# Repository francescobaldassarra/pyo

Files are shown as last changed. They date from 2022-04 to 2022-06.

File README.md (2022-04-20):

# Pyo
Robotic platform for emotional research in the human-robot interaction field.

-- EN --
Pyo is a low-cost robotic platform aimed at researchers working in the field of Human Robot Interaction. It is based on the Arduino platform and additive manufacturing production process (3D printing FDM). It is an easy-to-manage, accessible and customisable tool to research used to test emotional and expressive capacity of a social robot. The current version of Pyo is developed with a focus on non-verbal communication using facial expressions, auditory icons and body language.

The purpose of the research is to investigate how robots’ non-verbal communication can trigger an emotional response and to what extent expression and feeling are connected in a human-robot interaction.

-- IT --
Pyo è una piattaforma rrobotica low-cost per ricercatori che lavorano nel campo dell'interazione uomo-robot. Si basa sulla piattaforma Arduino e sul processo di produzione additiva (stampa 3D FDM). È uno strumento di ricerca facile da gestire, accessibile e personalizzabile utilizzato per testare le capacità emotive ed espressive di un robot sociale. La versione attuale di Pyo è sviluppata con un focus sulla comunicazione non-verbale utilizzando espressioni facciali, icone uditive e linguaggio del corpo.

Lo scopo della ricerca è quello di indagare come la comunicazione non verbale dei robot può innescare una risposta emotiva e in che misura l'espressione e il sentimento sono collegati in un'interazione uomo-robot.

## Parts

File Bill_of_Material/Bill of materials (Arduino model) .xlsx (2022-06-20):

What I need to reproduce Pyo platform with Arduino
Name | Quantity | Price (Eur) | Link (approximate) | Note
Arduino Mega 2560 | 1 | 39.9 | https://www.amazon.com/ARDUINO-MEGA-2560-REV3-A000067/dp/B0046AMGW0
Mega Proto shield | 1 | 5.8 | https://www.amazon.com/Treedix-Prototype-Solderable-BreadBoard-Compatible/dp/B08G1G7YDZ
Audio amplifier module digital 3W 5V | 1 | 5.9 | https://www.amazon.com/HiLetgo-Amplifier-Dual-Channel-Amplifiers-Potentiometer/dp/B01DKAI51M
MP3 Player module MicroSD | 1 | 5.9 | https://www.amazon.com/DFPlayer-Player-YX5200-Support-Arduino/dp/B07BDD8BF3
Micro SD (>1gb) | 1 | 4.4
IR emote Control, Sensor Board | 1 | 6.2 | https://www.amazon.com/KOOBOOK-Infrared-Wireless-Control-Receiver/dp/B07S67SFSF
Speaker | 1 | 7.1 | https://www.amazon.com/Fielect-Magnet-Speaker-Internal-Rectangle/dp/B08276866N
Servo motor MG996R | 4 | 24.7 | https://www.amazon.com/DaFuRui-Digital-Compatible-Arduino-Helicopter/dp/B09P18XNK2
Led matrix 8x32 RGB | 1 | 20.2 | https://www.amazon.com/BTF-LIGHTING-Individual-Addressable-Flexible-Controllers/dp/B088BTXHRG
Switch on/off | 1 | 1
Axial bearing 25x47x12 | 1 | 13.6 | https://www.amazon.com/Rubber-Sealed-Bearing-6900-2RS-10226mm/dp/B07KQS8D53 | I suggest to use 2 overlapping bearings or modify the 3d model (it is difficult to find one 12mm high but with 10mm hole)
Power supply 5V, 2A | 1 | 10 | https://www.amazon.com/-/en/dp/B01I1LRCXW
Eva rubber plates, 2mm | 1 | 8 | https://www.amazon.com/Sheets-Assorted-Better-Office-Products/dp/B091Y46B3Y
Fishing line | 1 | 3.8 | https://www.amazon.com/-/en/dp/B000HWY6QK/ref=sr_1_3?keywords=fiskelina&qid=1636623219&sr=8-3
Double-side tape | 1 | 2.6 | https://www.amazon.com/-/en/dp/B00ABKBOVS/ref=sr_1_7?keywords=dubbelsidig+tejp&qid=1636623296&sr=8-7
Rubber band 6mm | 1 | 2.6 | https://www.amazon.com/-/en/dp/B004WC1XB2/ref=sr_1_9?keywords=gummiband+6+mm&qid=1636629279&sr=8-9
PLA+ Sunlu |  | 18 | https://www.amazon.com/dp/B08CVG79JM/ref=twister_B0B1PQ2VRM?_encoding=UTF8&th=1
TPU black (0.5kg) | 1 | 24.6 | https://www.amazon.com/Filament-SUNLU-Flexible-Dimensional-Accuracy/dp/B08FT5KSBP
Cable and soldering stuff | 1 | n/d
Total |  | 204.3

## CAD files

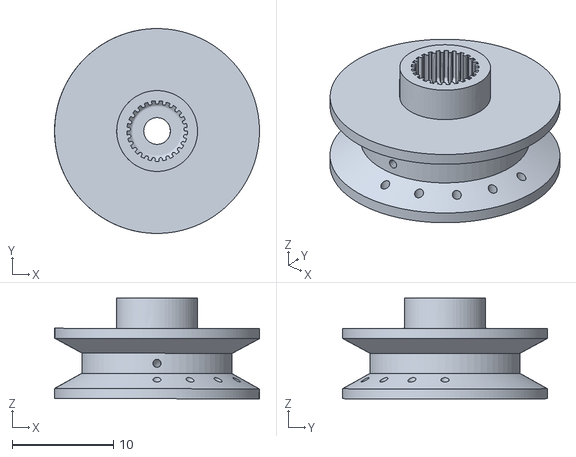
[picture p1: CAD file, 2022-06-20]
STL_file/Full_Body_version/9_PuleggiaT.stl
20.3 x 20.3 x 9.98

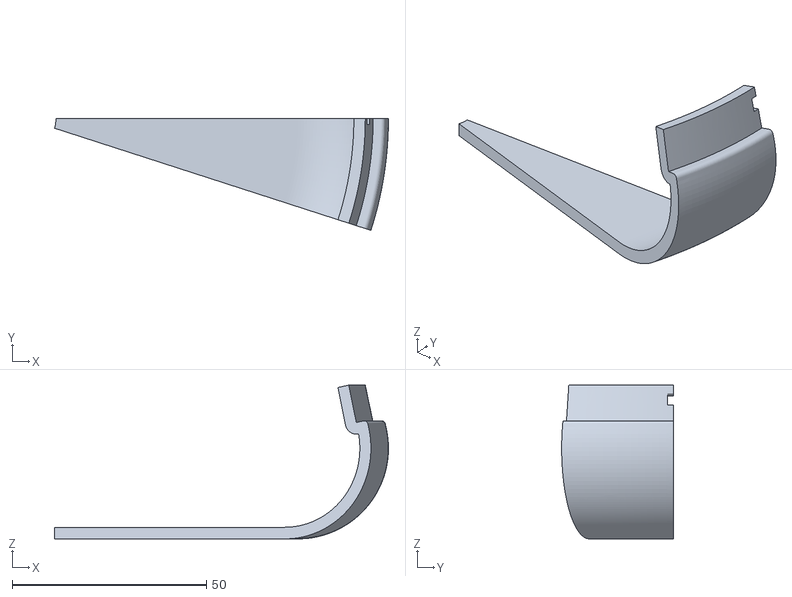
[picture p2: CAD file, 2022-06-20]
STL_file/Naked_version/prova_base_curva.stl
86.1 x 28.8 x 39.6

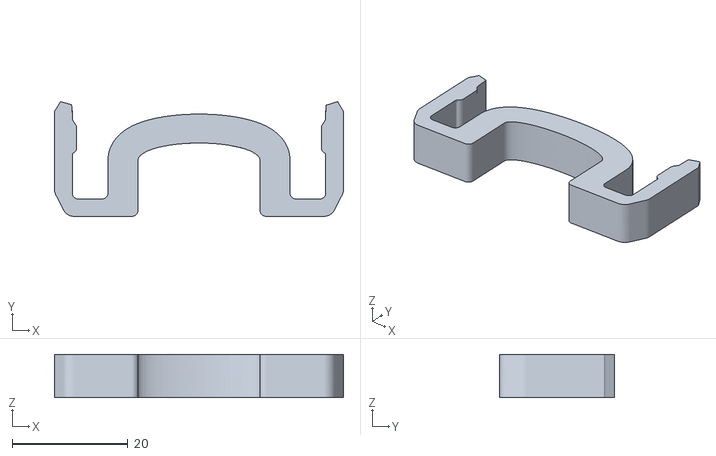
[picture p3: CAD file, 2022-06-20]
STL_file/Full_Body_version/11_Molla_tpu.stl
50.0 x 19.8 x 7.50

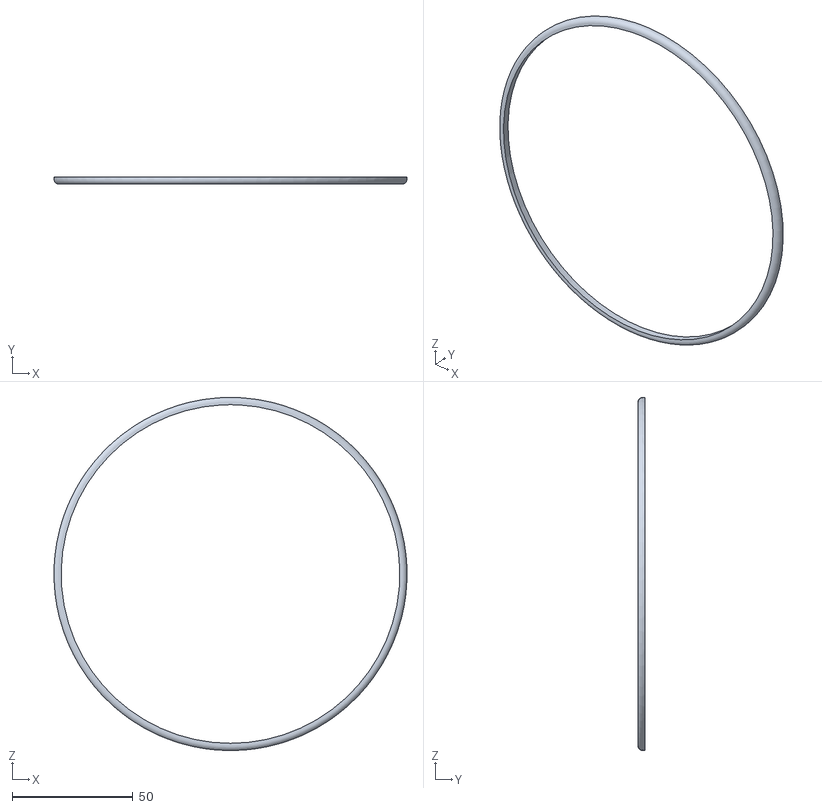
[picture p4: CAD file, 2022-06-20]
STL_file/Naked_version/circle_test.STL
146.0 x 3.00 x 146.0

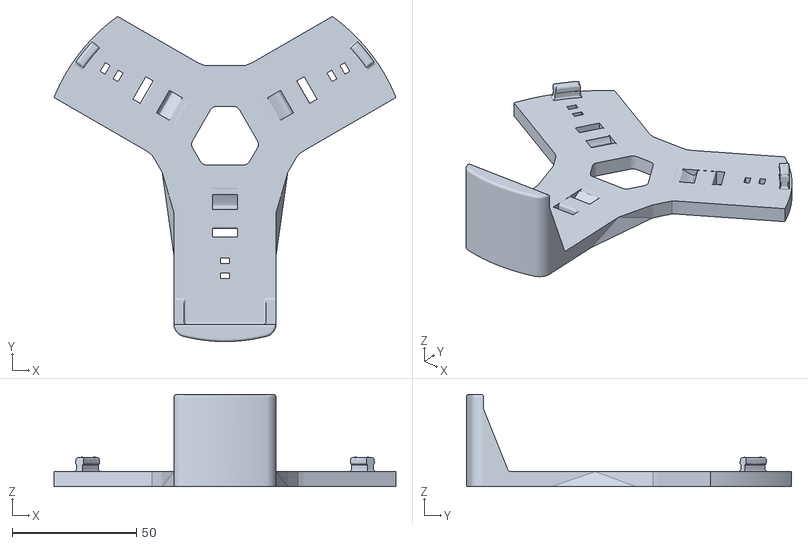
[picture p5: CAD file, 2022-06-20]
STL_file/Full_Body_version/5_TestaBase.stl
137.4 x 130.7 x 37.0

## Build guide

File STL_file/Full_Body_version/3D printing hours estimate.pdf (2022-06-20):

## 3D printing of Pyo (Arduino version)

### Estimate consumption of hours and materials for Pyo

Slicer SW: Ultimaker Cura
Printer: Prusa i3 MK3
Slicing: Normal resolution (0.15mm), default settings

### PLA (1,75mm white)

Part name | Quantity (gr) | Time | Preview

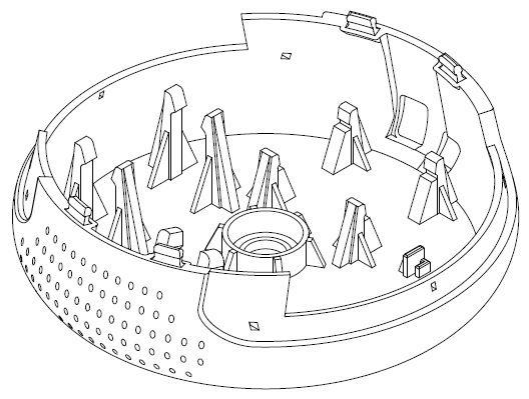
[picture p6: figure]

Base bottom | 138 | 17h

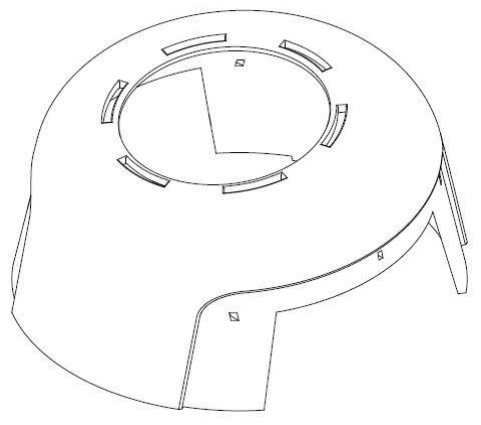
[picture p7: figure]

Base top | 95 | 11h

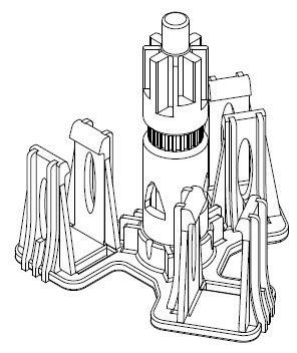
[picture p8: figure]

Motors housing | 48 | 7h

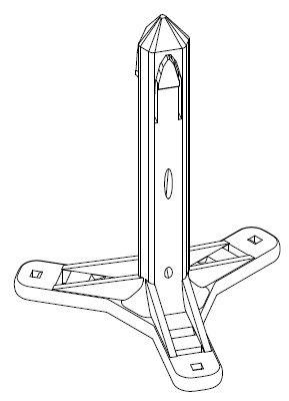
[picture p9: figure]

Head connection | 26 | 4h

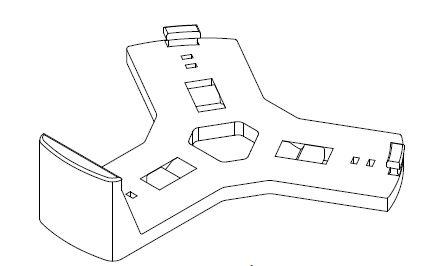
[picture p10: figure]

Head base 1 | 26 | 3h

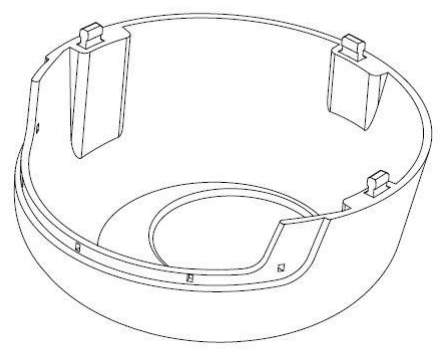
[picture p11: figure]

Head bottom | 74 | 9h

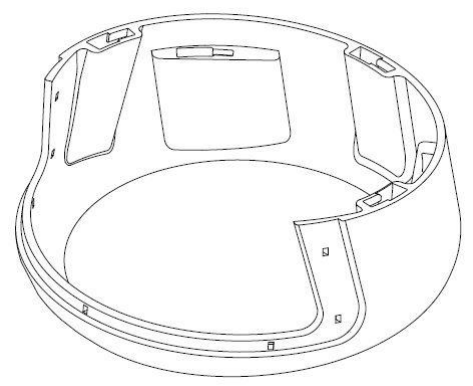
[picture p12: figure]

Head top | 105 | 12h

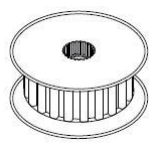
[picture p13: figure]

Pulley R | 2 | 24min

Pulley T (x3) | 3 | 40min
Total | 517 | 64h

### TPU (Sunlu 1,75mm flexible black tpu)

Part name | Quantity (gr) | Time | Preview

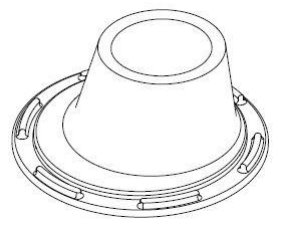
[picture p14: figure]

Neck | 26 | 3
Spring (x3) | 6 | 1
Total | 32 | 4

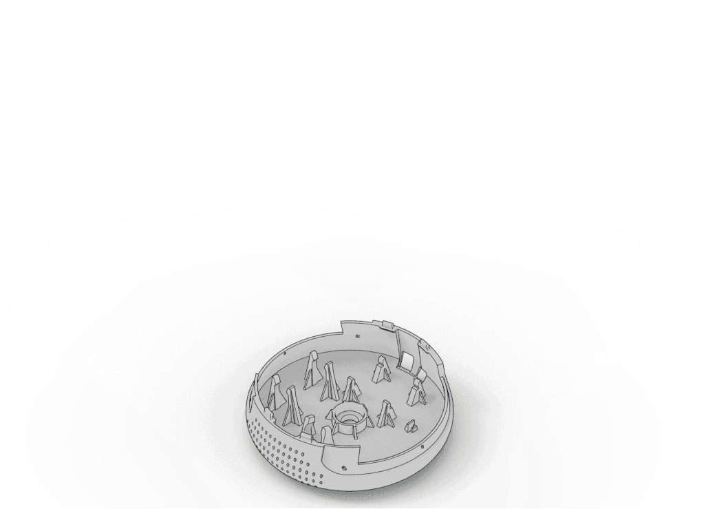
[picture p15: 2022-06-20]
Technical draw/Assembly.gif

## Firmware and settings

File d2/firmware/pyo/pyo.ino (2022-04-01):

/////////////////////////////////////////////////////////////////////// led screen _ matrix 8x32 ///////////////////////////////////////////////////////////////////////////////////

#include <Adafruit_NeoPixel.h>
#define schermo A4 // matrice 8x32
// Parameter 1 = number of pixels in strip
// Parameter 2 = pin number (most are valid)
// Parameter 3 = pixel type flags, add together as needed:
//   NEO_KHZ800  800 KHz bitstream (most NeoPixel products w/WS2812 LEDs)
//   NEO_KHZ400  400 KHz (classic 'v1' (not v2) FLORA pixels, WS2811 drivers)
//   NEO_GRB     Pixels are wired for GRB bitstream (most NeoPixel products)
//   NEO_RGB     Pixels are wired for RGB bitstream (v1 FLORA pixels, not v2)
Adafruit_NeoPixel strip = Adafruit_NeoPixel(256, schermo, NEO_GRB + NEO_KHZ800);


//////////////////////////////////////////////////////////////////////// MP3 _ speaker ////////////////////////////////////////////////////////////////////////////////////

#include "Arduino.h"
#include "SoftwareSerial.h"
#include "DFRobotDFPlayerMini.h"
SoftwareSerial mySoftwareSerial(11, 10); // RX, TX
DFRobotDFPlayerMini myDFPlayer;
void printDetail(uint8_t type, int value);

///////////////////////////////////////////////////////////////////////// Servo motor /////////////////////////////////////////////////////////////////////////////////////////////////////////

#include <Servo.h>
Servo Mrotation; 
Servo Mfront; 
Servo Mleft; 
Servo Mright; 
int pos = 0;

//////////////////////////////////////////////////////////////////////// IR _ controller //////////////////////////////////////////////////////////////////////////////////////

#include <IRremote.h>
int receiver = 34;
IRrecv irrecv(receiver);     // create instance of 'irrecv'
decode_results results;      // create instance of 'decode_results'

///////////////////////////////////////////////////////////////////////// potentiometer /////////////////////////////////////////////////////////////////////////////////////

int volumePIN  = A2;
int volume = 0;

int lumenPIN = A3;
int lumen = 0;

/////////////////////////////////////////////////////////////////////////////////////////////////////////////////////////////////////////////////////////////////////////////////////

void setup() {

  // IR controller
  irrecv.enableIRIn(); // Start the receiver


  // screen
  strip.begin();
  strip.setBrightness(255);
  strip.show();   // Initialize all pixels to 'off'
  showEyes(0);
  delay(300);


  // MP3 _ voice set up
  mySoftwareSerial.begin(9600);
  Serial.begin(115200);
  if (!myDFPlayer.begin(mySoftwareSerial)) {  //Use softwareSerial to communicate with mp3.
    Serial.println(F("Unable to begin:"));
    Serial.println(F("1.Please recheck the connection!"));
    Serial.println(F("2.Please insert the SD card!"));
    while (true);
  }
  Serial.println(F("DFPlayer Mini online."));

  myDFPlayer.volume(25);  //Set volume value. From 0 to 30
  myDFPlayer.play(0);


  //////////////////////////////////////////////////////////////////////////////////////

  // head motor  _ go to home position 0
  Mfront.attach(6);
  Mfront.write(0);// move servos to center position 0

  Mleft.attach(4);
  Mleft.write(0);// move servos to center position 0

  Mright.attach(2);
  Mright.write(0);// move servos to center position 0


  // rotation motor _ turn left and right
  Mrotation.attach(8);
  Mrotation.write (90);

  /*
    for (pos = 90; pos <= 180; pos += 1) { // look to the right
      Mrotation.write(pos);
      delay(5);
    }
    delay(500);

    for (pos = 180; pos >= 0; pos -= 1) { //look to the left
      Mrotation.write(pos);
      delay(6);
    }
    delay(500);

    for (pos = 0; pos <= 90; pos += 1) { // look ahead
      Mrotation.write(pos);
      delay(6);
    }
  */
}

void loop()
{

  /*  
      volume = analogRead(volumePIN);
      volume = map(volumePIN, 0, 1023, 0, 30); // check mp3 volume
      myDFPlayer.volume(volume);

      lumen = analogRead(lumenPIN);
      lumen = map(lumenPIN, 0, 1023, 0, 255); // check led brightness
      strip.setBrightness(lumen);

  */

  if (irrecv.decode(&results)) // have we received an IR signal?
  {
    translateIR();
    irrecv.resume(); // receive the next value
  }
}

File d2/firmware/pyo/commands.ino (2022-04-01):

uint8_t neutral[] = {
  0x00000000, 0x00000000, 0x00000000, 0x00000000, 0x00000000, 0x00000000, 0x00000000, 0x00000000,
  0x00000000, 0x00000000, 0x00000000, 0x00000000, 0x00000000, 0x00000000, 0x00000000, 0x00000000,
  0x00000000, 0x00000000, 0x00000000, 0x00000000, 0x00000000, 0x00000000, 0x00000000, 0x00000000,
  0x00000000, 0x00000000, 0x00000000, 0x00000000, 0x00000000, 0x00000000, 0x00000000, 0x00000000,
  0x00000000, 0x00000000, 0x00000000, 0x00000000, 0x00000000, 0x00000000, 0x00000000, 0x00000000,
  0x00000000, 0x00000000, 0x00000000, 0x00000000, 0x00000000, 0x00000000, 0x00000000, 0x00000000,
  0x00000000, 0x00000000, 0x00000000, 0x00000000, 0x00000000, 0x00000000, 0x00000000, 0x00000000,
  0x00000000, 0x00000000, 0x00000000, 0x00000000, 0x00000000, 0x00000000, 0x00000000, 0x00000000,
  0x00000000, 0x00000000, 0x00000000, 0x00000000, 0x00000000, 0x00000000, 0x00000000, 0x00000000,
  0x00000000, 0x00000000, 0x00FFFFFF, 0x00FFFFFF, 0x00FFFFFF, 0x00000000, 0x00000000, 0x00000000,
  0x00000000, 0x00000000, 0x00FFFFFF, 0x00000000, 0x00000000, 0x00000000, 0x00FFFFFF, 0x00000000,
  0x00000000, 0x00FFFFFF, 0x00000000, 0x00000000, 0x00000000, 0x00FFFFFF, 0x00000000, 0x00000000,
  0x00000000, 0x00000000, 0x00FFFFFF, 0x00000000, 0x00000000, 0x00000000, 0x00FFFFFF, 0x00000000,
  0x00000000, 0x00000000, 0x00FFFFFF, 0x00FFFFFF, 0x00FFFFFF, 0x00000000, 0x00000000, 0x00000000,
  0x00000000, 0x00000000, 0x00000000, 0x00000000, 0x00000000, 0x00000000, 0x00000000, 0x00000000,
  0x00000000, 0x00000000, 0x00000000, 0x00000000, 0x00000000, 0x00000000, 0x00000000, 0x00000000,
  0x00000000, 0x00000000, 0x00000000, 0x00000000, 0x00000000, 0x00000000, 0x00000000, 0x00000000,
  0x00000000, 0x00000000, 0x00000000, 0x00000000, 0x00000000, 0x00000000, 0x00000000, 0x00000000,
  0x00000000, 0x00000000, 0x00000000, 0x00FFFFFF, 0x00FFFFFF, 0x00FFFFFF, 0x00000000, 0x00000000,
  0x00000000, 0x00FFFFFF, 0x00000000, 0x00000000, 0x00000000, 0x00FFFFFF, 0x00000000, 0x00000000,
  0x00000000, 0x00000000, 0x00FFFFFF, 0x00000000, 0x00000000, 0x00000000, 0x00FFFFFF, 0x00000000,
  0x00000000, 0x00FFFFFF, 0x00000000, 0x00000000, 0x00000000, 0x00FFFFFF, 0x00000000, 0x00000000,
  0x00000000, 0x00000000, 0x00000000, 0x00FFFFFF, 0x00FFFFFF, 0x00FFFFFF, 0x00000000, 0x00000000,
  0x00000000, 0x00000000, 0x00000000, 0x00000000, 0x00000000, 0x00000000, 0x00000000, 0x00000000,
  0x00000000, 0x00000000, 0x00000000, 0x00000000, 0x00000000, 0x00000000, 0x00000000, 0x00000000,
  0x00000000, 0x00000000, 0x00000000, 0x00000000, 0x00000000, 0x00000000, 0x00000000, 0x00000000,
  0x00000000, 0x00000000, 0x00000000, 0x00000000, 0x00000000, 0x00000000, 0x00000000, 0x00000000,
  0x00000000, 0x00000000, 0x00000000, 0x00000000, 0x00000000, 0x00000000, 0x00000000, 0x00000000,
  0x00000000, 0x00000000, 0x00000000, 0x00000000, 0x00000000, 0x00000000, 0x00000000, 0x00000000,
  0x00000000, 0x00000000, 0x00000000, 0x00000000, 0x00000000, 0x00000000, 0x00000000, 0x00000000,
  0x00000000, 0x00000000, 0x00000000, 0x00000000, 0x00000000, 0x00000000, 0x00000000, 0x00000000,
  0x00000000, 0x00000000, 0x00000000, 0x00000000, 0x00000000, 0x00000000, 0x00000000, 0x00000000,
};



uint8_t joy [] = {
  0x00000000, 0x00000000, 0x00000000, 0x00000000, 0x00000000, 0x00000000, 0x00000000, 0x00000000,
  0x00000000, 0x00000000, 0x00000000, 0x00000000, 0x00000000, 0x00000000, 0x00000000, 0x00000000,
  0x00000000, 0x00000000, 0x00000000, 0x00000000, 0x00000000, 0x00000000, 0x00000000, 0x00000000,
  0x00000000, 0x00000000, 0x00000000, 0x00000000, 0x00000000, 0x00000000, 0x00000000, 0x00000000,
  0x00000000, 0x00000000, 0x00000000, 0x00000000, 0x00000000, 0x00000000, 0x00000000, 0x00000000,
  0x00000000, 0x00000000, 0x00000000, 0x00000000, 0x00000000, 0x00000000, 0x00000000, 0x00000000,
  0x00000000, 0x00000000, 0x00000000, 0x00000000, 0x00000000, 0x00000000, 0x00000000, 0x00000000,
  0x00000000, 0x00000000, 0x00000000, 0x00000000, 0x00000000, 0x00000000, 0x00000000, 0x00000000,
  0x00000000, 0x00000000, 0x00000000, 0x00000000, 0x00000000, 0x00000000, 0x00000000, 0x00000000,
  0x00000000, 0x00000000, 0x00000000, 0x000088FF, 0x00000000, 0x00000000, 0x00000000, 0x00000000,
  0x00000000, 0x00000000, 0x00000000, 0x00000000, 0x00000000, 0x000088FF, 0x00000000, 0x00000000,
  0x00000000, 0x00000000, 0x000088FF, 0x00000000, 0x00000000, 0x00000000, 0x00000000, 0x00000000,
  0x00000000, 0x00000000, 0x00000000, 0x00000000, 0x00000000, 0x000088FF, 0x00000000, 0x00000000,
  0x00000000, 0x00000000, 0x00000000, 0x000088FF, 0x00000000, 0x00000000, 0x00000000, 0x00000000,
  0x00000000, 0x00000000, 0x00000000, 0x00000000, 0x00000000, 0x00000000, 0x00000000, 0x00000000,
  0x00000000, 0x00000000, 0x00000000, 0x00000000, 0x00000000, 0x00000000, 0x00000000, 0x00000000,
  0x00000000, 0x00000000, 0x00000000, 0x00000000, 0x00000000, 0x00000000, 0x00000000, 0x00000000,
  0x00000000, 0x00000000, 0x00000000, 0x00000000, 0x00000000, 0x00000000, 0x00000000, 0x00000000,
  0x00000000, 0x00000000, 0x00000000, 0x00000000, 0x000088FF, 0x00000000, 0x00000000, 0x00000000,
  0x00000000, 0x00000000, 0x000088FF, 0x00000000, 0x00000000, 0x00000000, 0x00000000, 0x00000000,
  0x00000000, 0x00000000, 0x00000000, 0x00000000, 0x00000000, 0x000088FF, 0x00000000, 0x00000000,
  0x00000000, 0x00000000, 0x000088FF, 0x00000000, 0x00000000, 0x00000000, 0x00000000, 0x00000000,
  0x00000000, 0x00000000, 0x00000000, 0x00000000, 0x000088FF, 0x00000000, 0x00000000, 0x00000000,
  0x00000000, 0x00000000, 0x00000000, 0x00000000, 0x00000000, 0x00000000, 0x00000000, 0x00000000,
  0x00000000, 0x00000000, 0x00000000, 0x00000000, 0x00000000, 0x00000000, 0x00000000, 0x00000000,
  0x00000000, 0x00000000, 0x00000000, 0x00000000, 0x00000000, 0x00000000, 0x00000000, 0x00000000,
  0x00000000, 0x00000000, 0x00000000, 0x00000000, 0x00000000, 0x00000000, 0x00000000, 0x00000000,
  0x00000000, 0x00000000, 0x00000000, 0x00000000, 0x00000000, 0x00000000, 0x00000000, 0x00000000,
  0x00000000, 0x00000000, 0x00000000, 0x00000000, 0x00000000, 0x00000000, 0x00000000, 0x00000000,
  0x00000000, 0x00000000, 0x00000000, 0x00000000, 0x00000000, 0x00000000, 0x00000000, 0x00000000,
  0x00000000, 0x00000000, 0x00000000, 0x00000000, 0x00000000, 0x00000000, 0x00000000, 0x00000000,
  0x00000000, 0x00000000, 0x00000000, 0x00000000, 0x00000000, 0x00000000, 0x00000000, 0x00000000,
};
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

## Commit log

2022-04-01 changed folder name and fixed issue on pos 1
    [commands.ino, pyo.ino]
2022-06-20 add file to assembly and print the full body version and a naked version
    [11_Molla_tpu.stl, 5_TestaBase.stl, 9_PuleggiaT.stl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]
2022-06-20 Create Bill of materials (Arduino model) .xlsx
    [Bill of materials (Arduino model) .xlsx]
2022-06-20 add note about use of bearings
    [Bill of materials (Arduino model) .xlsx]
